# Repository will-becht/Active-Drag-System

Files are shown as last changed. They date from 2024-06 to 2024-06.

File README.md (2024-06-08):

# Active Drag System

## Table of Contents
- [Introduction](#introduction)
- [Flight Software](#flight-software)
- [PCB Design](#pcb-design)
- [OpenRocket](#openrocket)
- [CAD](#cad)
- [Installation](#installation)

## Introduction
This project is focused on the development of an active drag system, or air brake, for a model rocket competing in the NASA Student Launch competition (https://www.nasa.gov/learning-resources/nasa-student-launch/). This work was done on a non-competition vehicle as its advancements are intended to be used in future years' competitions.
This project demonstrates the designs of the various components, including the flight software, printed circuit board (PCB), OpenRocket analysis for the vehicle, and CAD drawings for the system. 
Due to time constraints and a focus on the main competition vehicle, the non-competition vehicle was never flown with an active drag system installed.

## Flight Software
### Overview
The `Arduino Codes` directory contains the code necessary for controlling the vehicle's Active Drag System. This system adjusts the vehicle's drag tabs based on readings from an altimeter and accelerometer to control the vehicle's apogee. The system is controlled before launch using a Bluetooth module that can connect to a user's phone, allowing for the constant monitoring of flight readiness once the system is installed in the vehicle. Data is redundantly saved to an onboard flash memory chip and SD for storage and post-flight analysis.

### Block Diagram
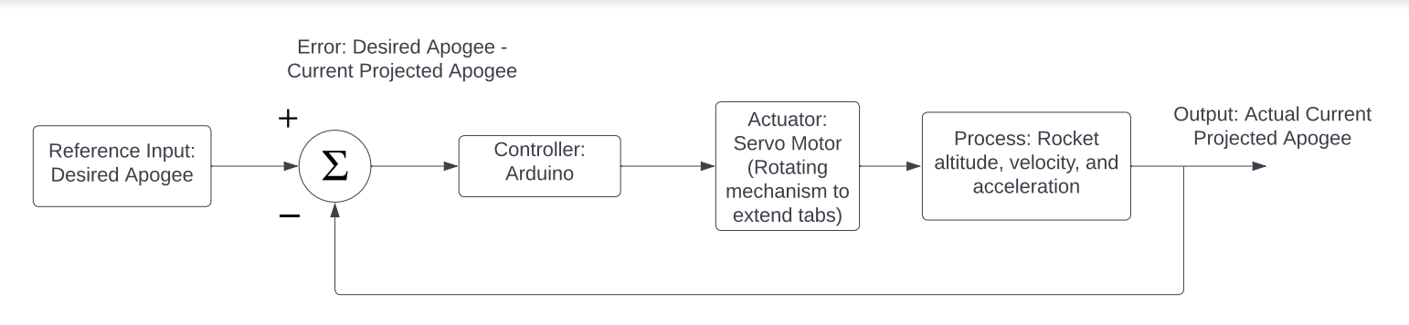
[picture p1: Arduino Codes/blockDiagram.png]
Flight Software


### Description
The flight software implements a state machine to manage the deployment of drag tabs in the Active Drag System. This system actively modulates the drag during flight to achieve a desired apogee by processing real-time data from the altimeter and accelerometer. The state machine ensures that the drag tabs are deployed or retracted based on the vehicle's altitude and acceleration, thus controlling the peak altitude accurately.

## PCB Design
### Overview
The `PCB Design` directory contains all the files related to the design and manufacturing of the vehicle's printed circuit boards (PCBs). These PCBs are used to integrate the electronic components necessary for the vehicle's operation.

### Images
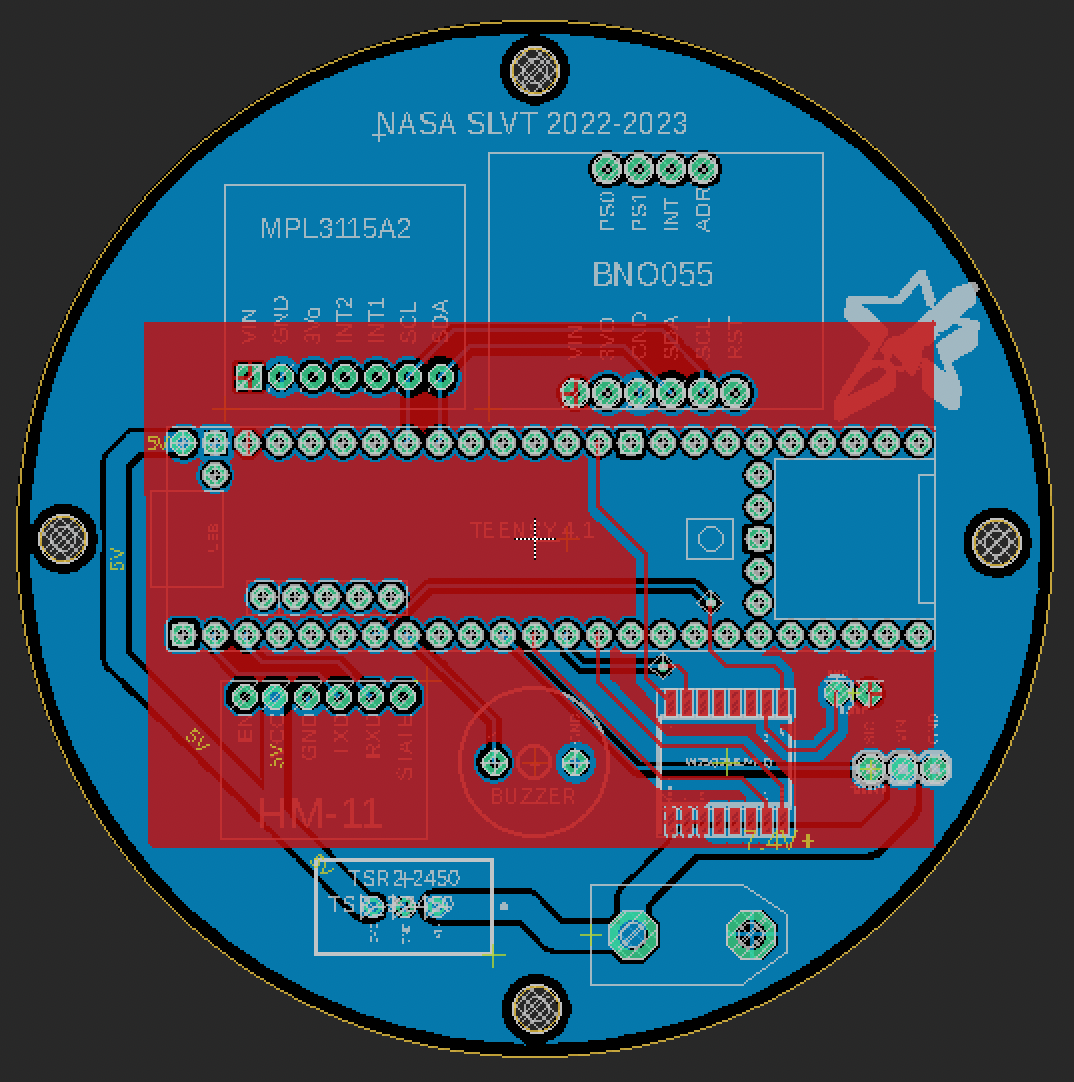
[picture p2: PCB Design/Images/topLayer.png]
Top Layer

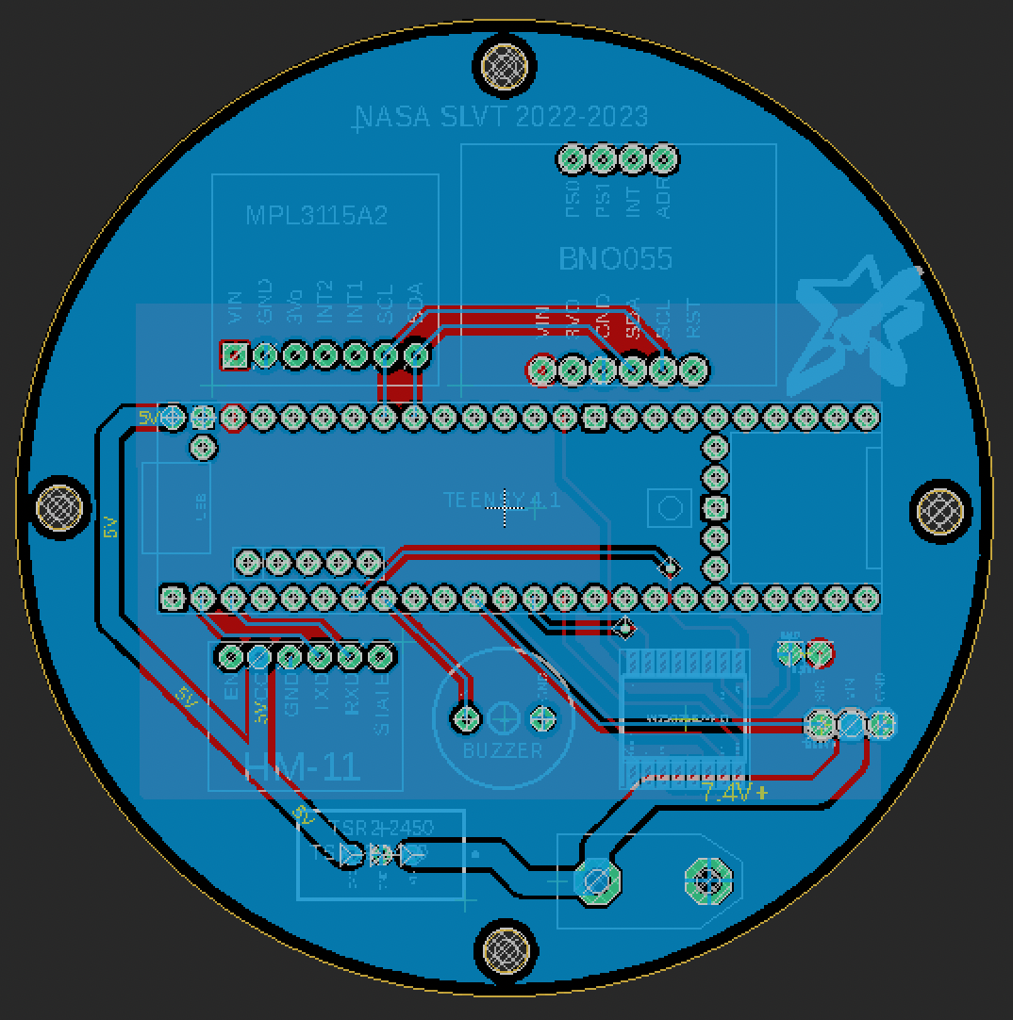
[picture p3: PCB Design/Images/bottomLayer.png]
Bottom Layer

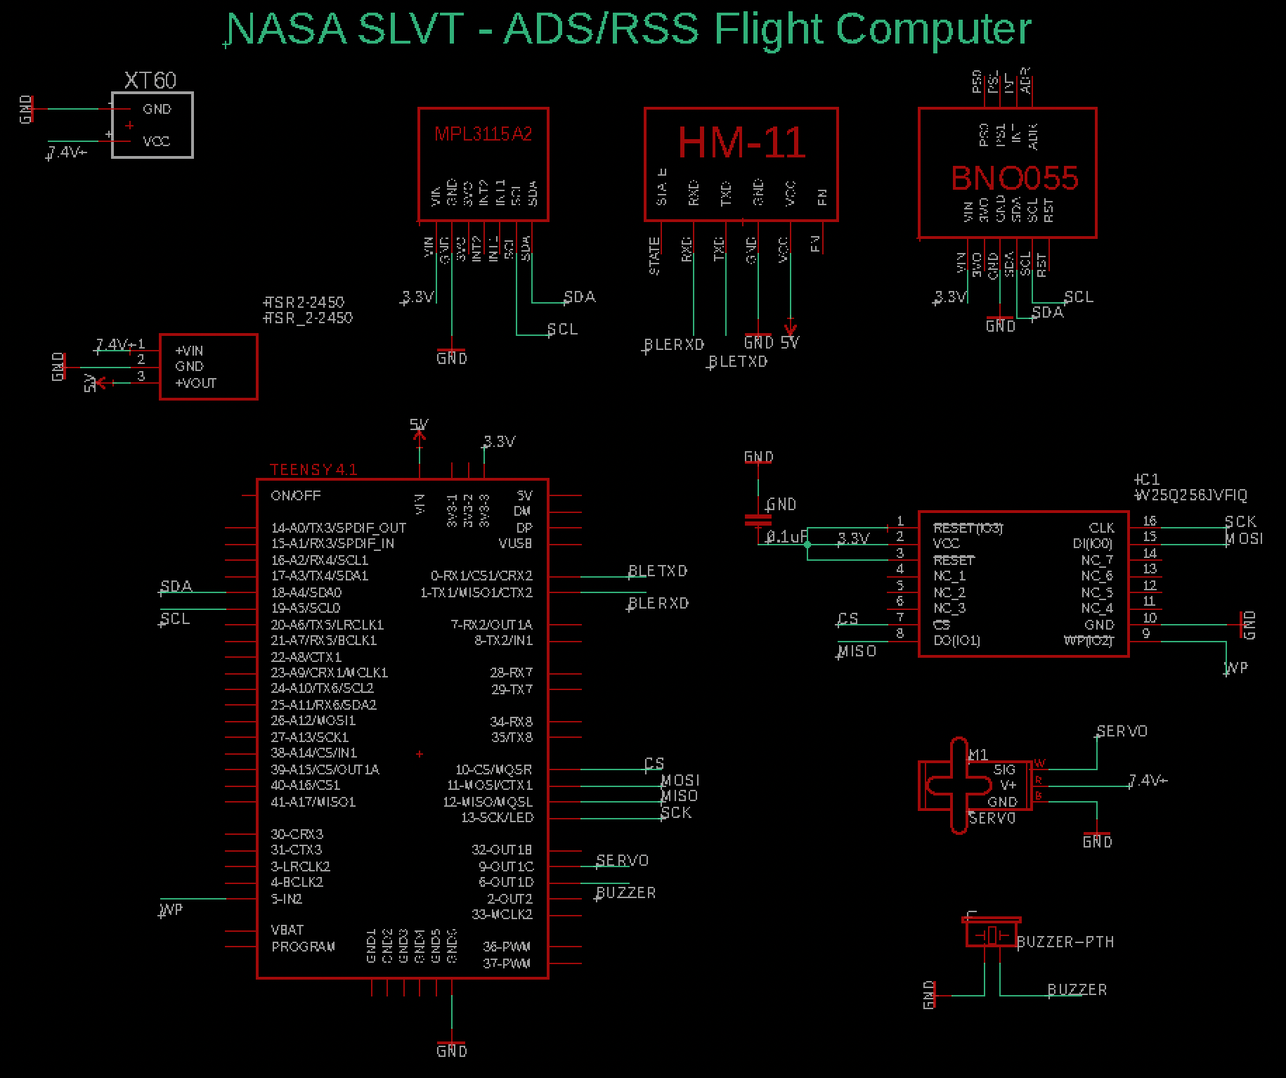
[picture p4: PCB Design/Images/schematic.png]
Schematic


### Description
PCB design is crucial for ensuring that the electronic components are connected properly. The files in this directory include design files, Gerber files for manufacturing, libraries for making the schematics, and images showing different layers and the schematic of the PCB. 

## OpenRocket
### Overview
The `OpenRocket` directory contains simulation files for the vehicle. These files can be used to simulate the vehicle's flight characteristics and performance.

### Images
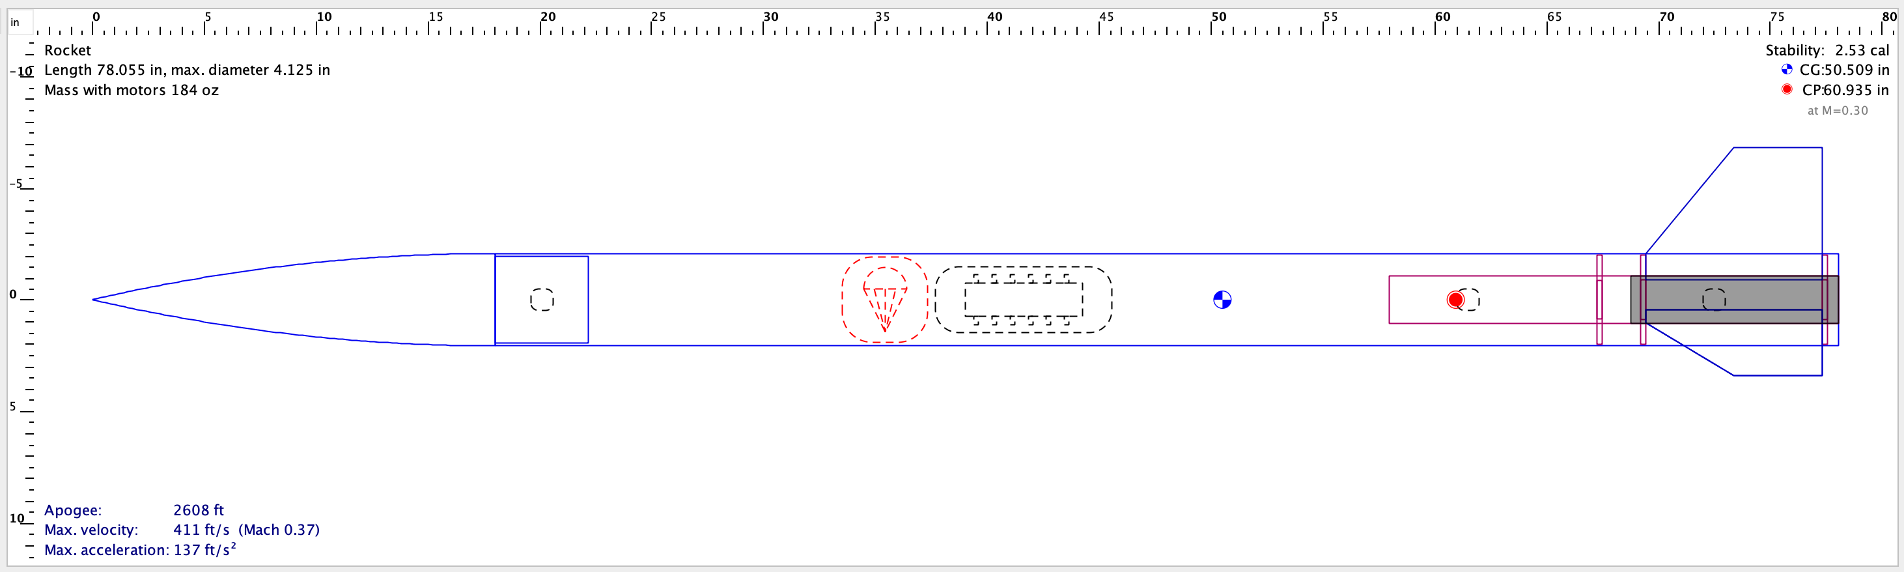
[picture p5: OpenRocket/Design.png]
Vehicle Design

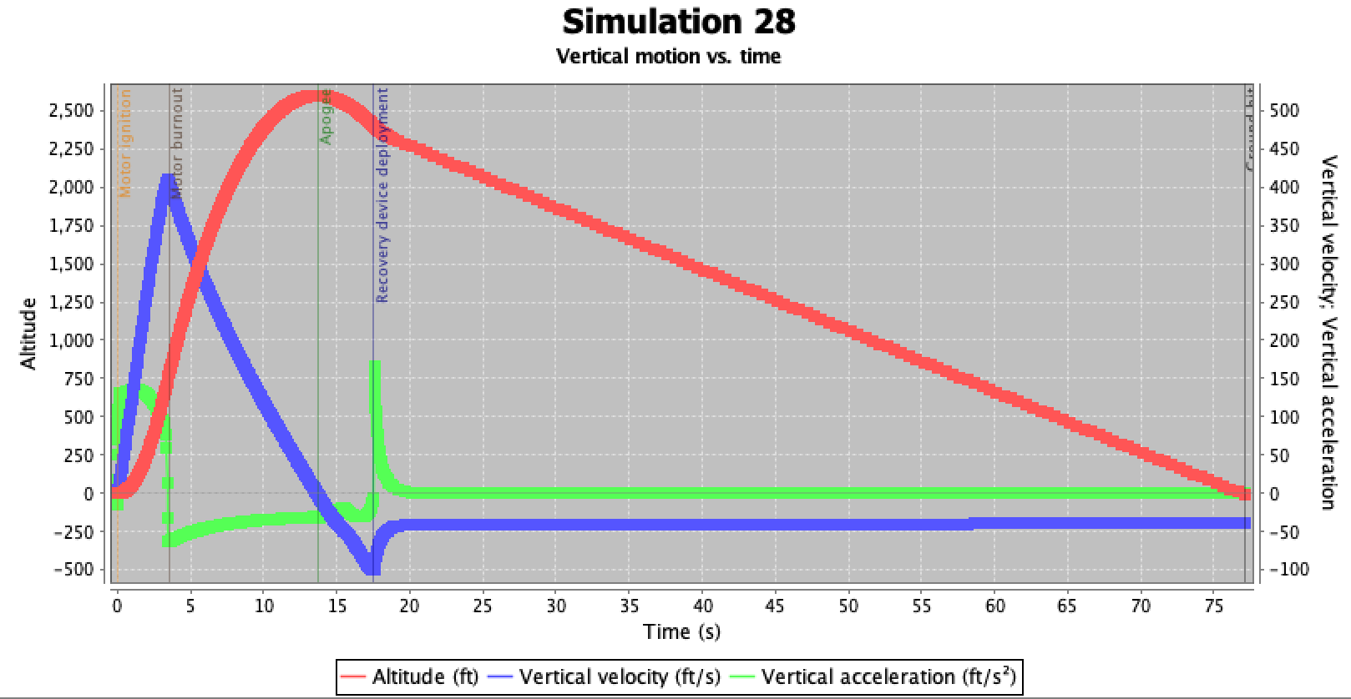
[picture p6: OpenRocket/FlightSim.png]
Flight Simulation


### Description
OpenRocket is a model rocket simulator that allows you to design and simulate the performance of rockets. The model in this directory represents the vehicle design as well as detailed simulations that help in predicting the flight path, stability, and performance of the vehicle.

## CAD
### Overview
The `CAD` directory contains the design files for the system's structural components. This model was created in SolidWorks, and the files can be used to fabricate the parts using 3D printing.

### Images
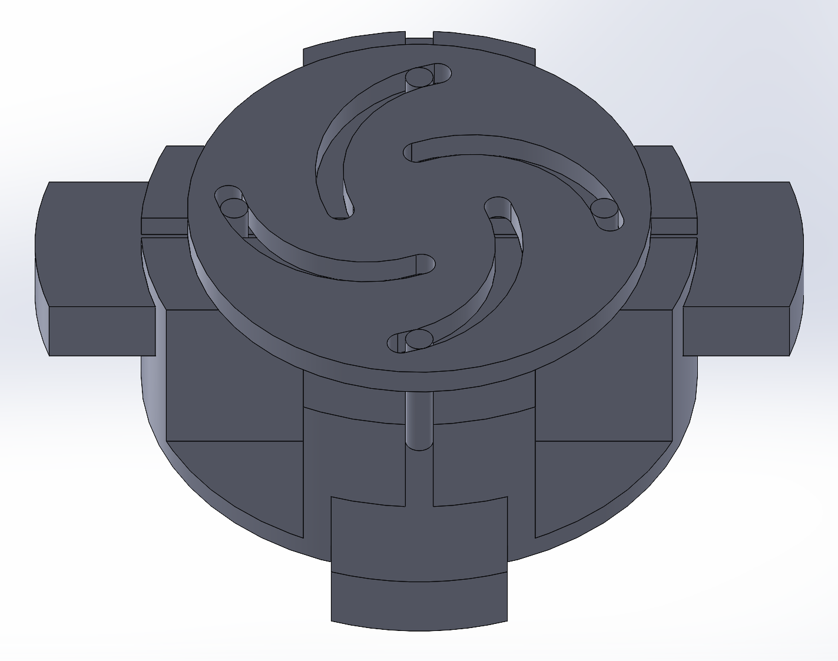
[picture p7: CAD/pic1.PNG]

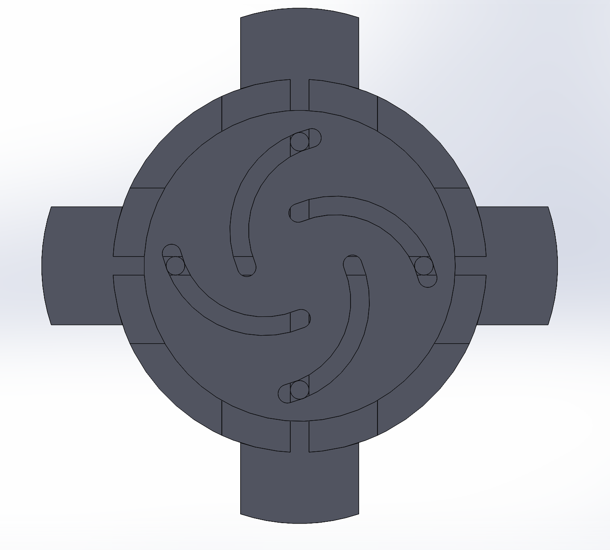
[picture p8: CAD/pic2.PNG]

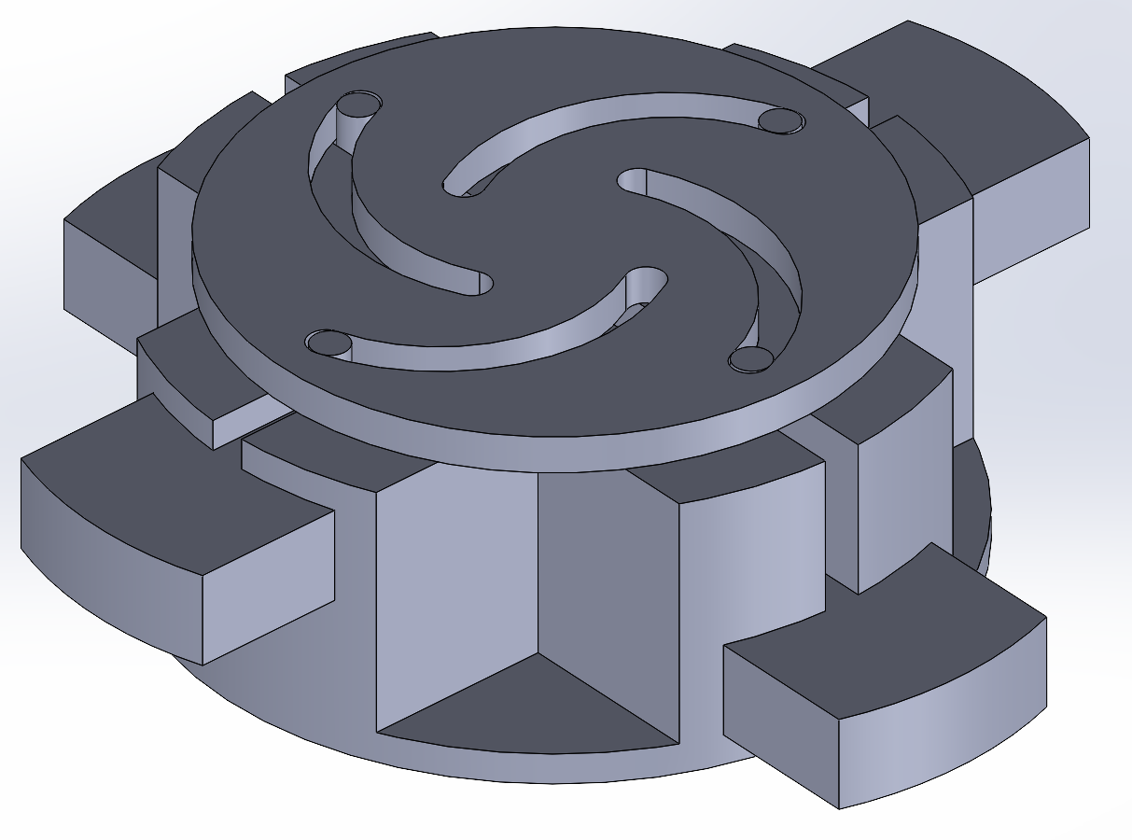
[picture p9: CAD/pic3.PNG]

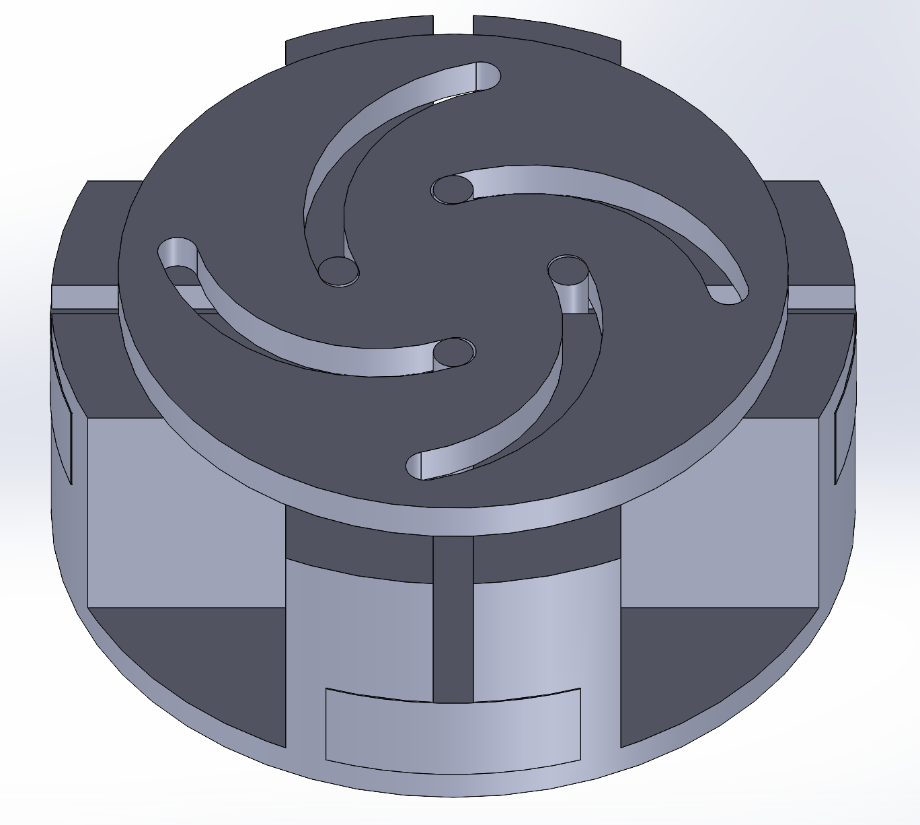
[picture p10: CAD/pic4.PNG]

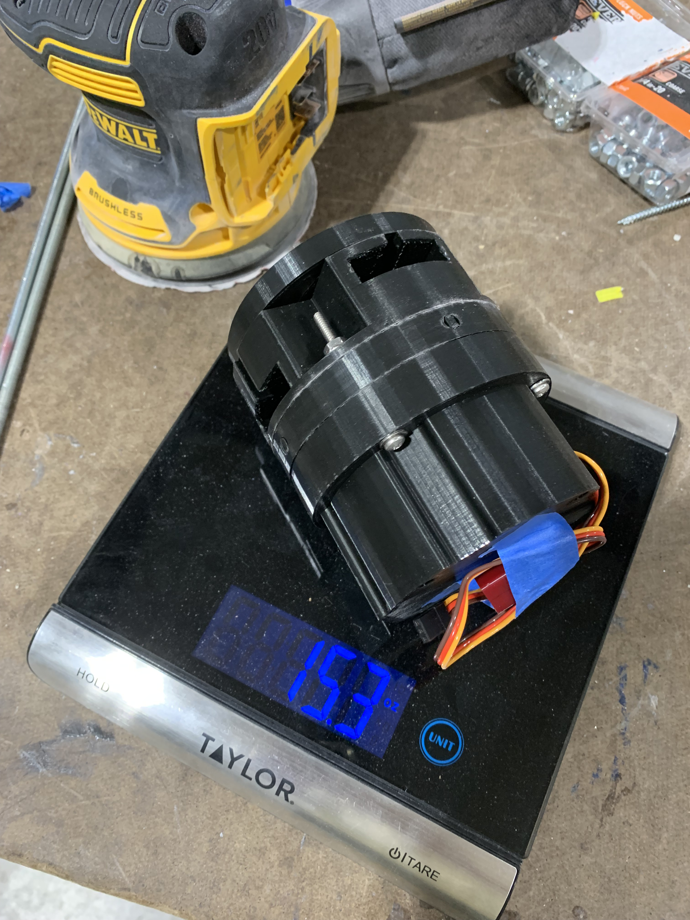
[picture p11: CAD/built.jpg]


### Description
FEA (finite element analysis) and CFD (computational fluid dynamics) were performed on the system to evaluate both its structural integrity and effectiveness as a braking system.

## Installation
To install the software and code for this project, follow these steps:

1. Clone the repository:
   ```bash
   git clone https://github.com/will-becht/Active-Drag-System

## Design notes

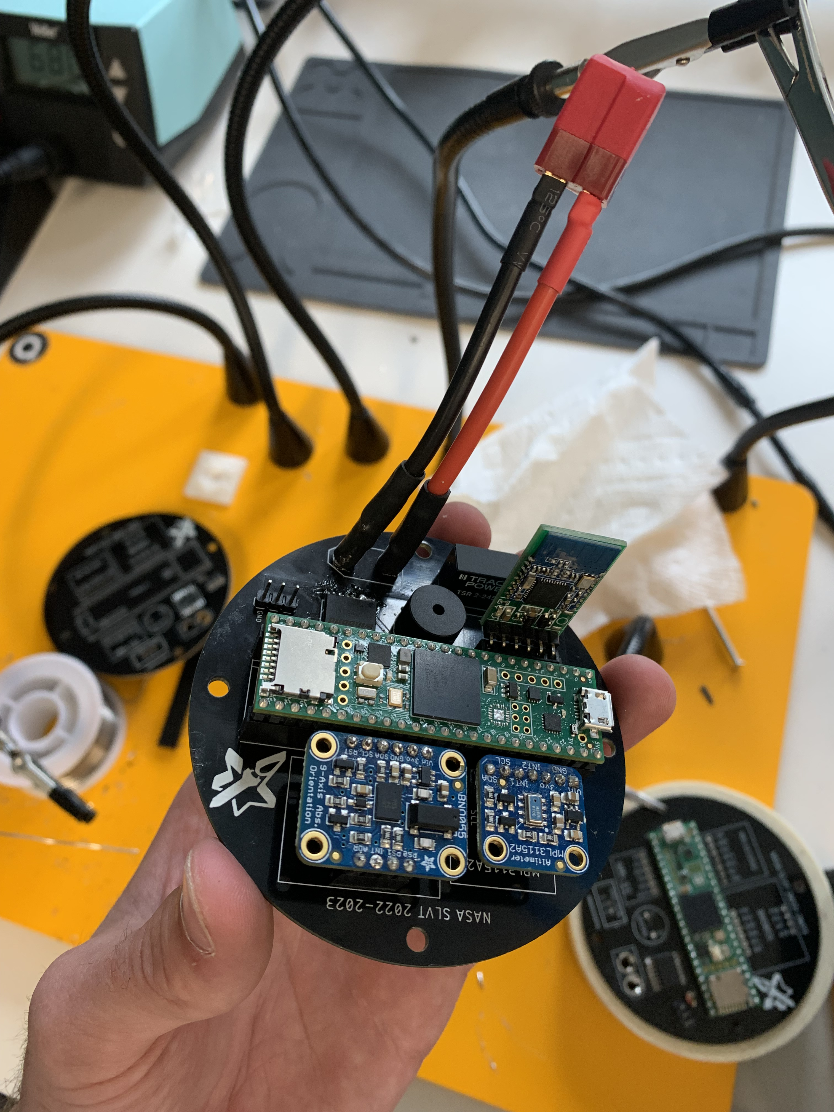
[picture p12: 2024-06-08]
PCB Design/Images/built.jpg

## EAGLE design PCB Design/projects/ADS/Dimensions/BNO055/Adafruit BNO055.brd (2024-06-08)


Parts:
C1, C2: 22pF; 0805-NO
C3: 0.1uF; 0805-NO
C4: 0.1uF; 0805_10MGAP
C5: 10uF; 0805-NO
C6: 10uF; 0805_10MGAP
D1: 1n4148; SOD-323
FID1, FID2: FIDUCIAL""; FIDUCIAL_1MM
JP1: HEADER-1X676MIL; 1X06_ROUND_76
JP2: HEADER-1X476MIL; 1X04_ROUND_76
Q1, Q2: BSS138; SOT23-WIDE
R3, R4, R5, R6, R7, R10: 10K; 0805-NO
R8, R9: 10K; _0805MP
U1: MIC5225-3.3; SOT23-5
U$2: BNO055
U$29, U$30, U$31, U$32: MOUNTINGHOLE2.5_THICK; MOUNTINGHOLE_2.5_PLATED_THICK
Y1: 32.768kHz; CRYSTAL_8X3.8

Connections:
3.3V: C4.2, C6.1, JP1.2, Q1.1 (G), Q2.1 (G), R6.2, R7.2, R10.2, U1.5 (OUT), U$2.3 (VDD), U$2.4 (NBOOT_LOAD_PIN), U$2.28 (VDDIO)
5.0V: C5.1, JP1.1, R8.2, R9.2, U1.1 (IN), U1.3 (EN)
GND: C1.1, C2.1, C3.1, C4.1, C5.2, C6.2, JP1.3, R3.2, R4.2, R5.2, U1.2 (GND), U$2.2 (GND), U$2.10 (PIN10(GND)), U$2.15 (PIN15(GND)), U$2.16 (PIN16(GND)), U$2.18 (COM2(GND)), U$2.25 (GND)
I2CADDR_3V: JP2.4, R5.1, U$2.17 (COM3/I2C_ADDR)
INT_3V: JP2.3, U$2.14 (INT)
unnamed: C1.2, U$2.27 (XIN32), Y1.P$4 (2)
unnamed: C2.2, U$2.26 (XOUT32), Y1.P$1 (1)
unnamed: C3.2, U$2.9 (CAP)
NRESET_3V: D1.A, R10.1, U$2.11 (NRESET)
PS0_3V: JP2.1, R3.1, U$2.6 (PS0)
PS1_3V: JP2.2, R4.1, U$2.5 (PS1)
RST_5V: D1.C, JP1.6
SCL_3V: Q2.2 (S), R7.1, U$2.19 (COM1/SCL/RX)
SCL_5V: JP1.5, Q2.3 (D), R9.1
SDA_3V: Q1.2 (S), R6.1, U$2.20 (COM0/SDA/TX)
SDA_5V: JP1.4, Q1.3 (D), R8.1



Board: 2 copper layers, 26.7 x 20.3 mm, 31 parts (2 on the bottom side), 16 nets.

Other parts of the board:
U$3: PCBFEAT-REV-040
U$28: ADAFRUIT_TEXT_20MM
U$33: ADAFRUIT_2.5MM

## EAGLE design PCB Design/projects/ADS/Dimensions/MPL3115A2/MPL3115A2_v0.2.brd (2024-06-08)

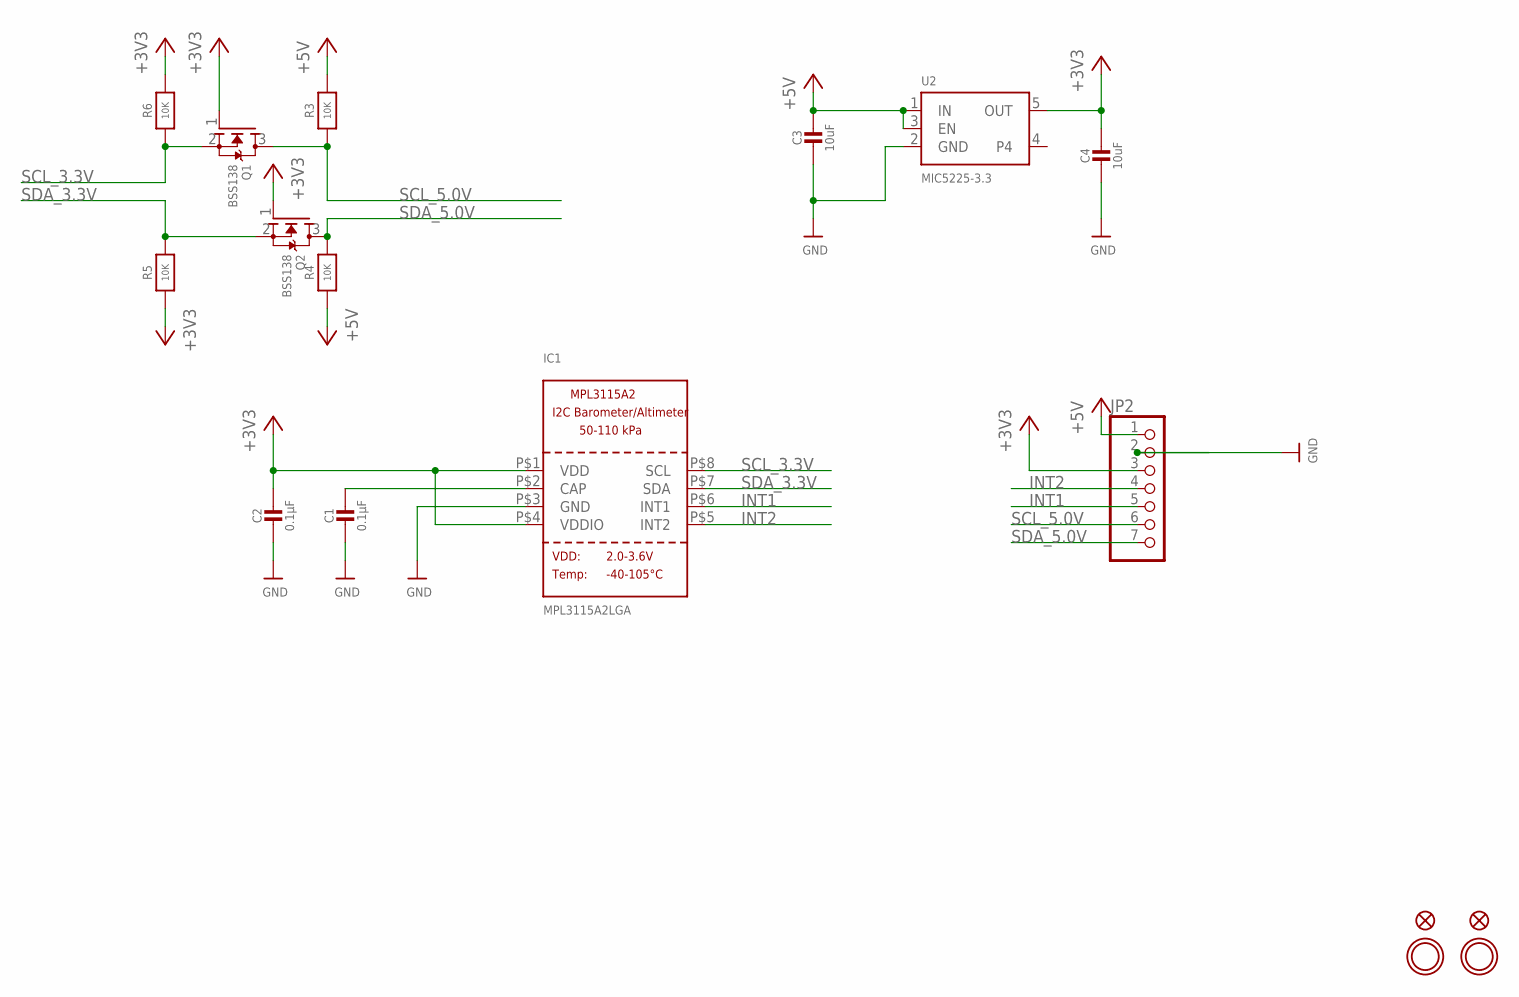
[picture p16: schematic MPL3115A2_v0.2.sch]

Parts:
C1, C2: 0.1µF; 0805-NO
C3, C4: 10uF; 0805-NO
FID1, FID2: FIDUCIAL""; FIDUCIAL_1MM
IC1: MPL3115A2LGA; LGA8
JP2: HEADER-1X770MIL; 1X07_ROUND_70
Q1, Q2: BSS138; SOT23-WIDE
R3, R4, R5, R6: 10K; 0805-NO
U2: MIC5225-3.3; SOT23-5
U$8, U$9: MOUNTINGHOLE2.5; MOUNTINGHOLE_2.5_PLATED

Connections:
+3V3: C2.1, C4.1, IC1.P$1 (VDD), IC1.P$4 (VDDIO), JP2.3, Q1.1 (G), Q2.1 (G), R5.1, R6.2, U2.5 (OUT)
+5V: C3.1, JP2.1, R3.2, R4.1, U2.1 (IN), U2.3 (EN)
CAP: C1.1, IC1.P$2 (CAP)
GND: C1.2, C2.2, C3.2, C4.2, IC1.P$3 (GND), JP2.2, U2.2 (GND)
INT1: IC1.P$6 (INT1), JP2.5
INT2: IC1.P$5 (INT2), JP2.4
SCL_3.3V: IC1.P$8 (SCL), Q1.2 (S), R6.1
SCL_5.0V: JP2.6, Q1.3 (D), R3.1
SDA_3.3V: IC1.P$7 (SDA), Q2.2 (S), R5.2
SDA_5.0V: JP2.7, Q2.3 (D), R4.2

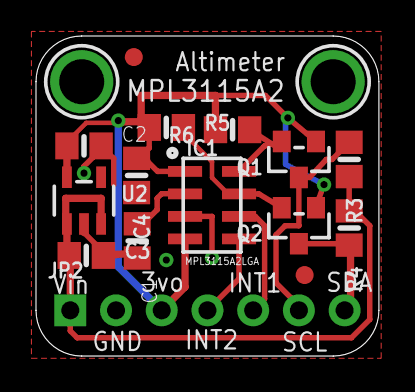
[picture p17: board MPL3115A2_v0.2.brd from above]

Board: 2 copper layers, 19.1 x 17.8 mm, 18 parts (1 on the bottom side), 10 nets.

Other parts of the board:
U$14: ADAFRUIT_3.5MM

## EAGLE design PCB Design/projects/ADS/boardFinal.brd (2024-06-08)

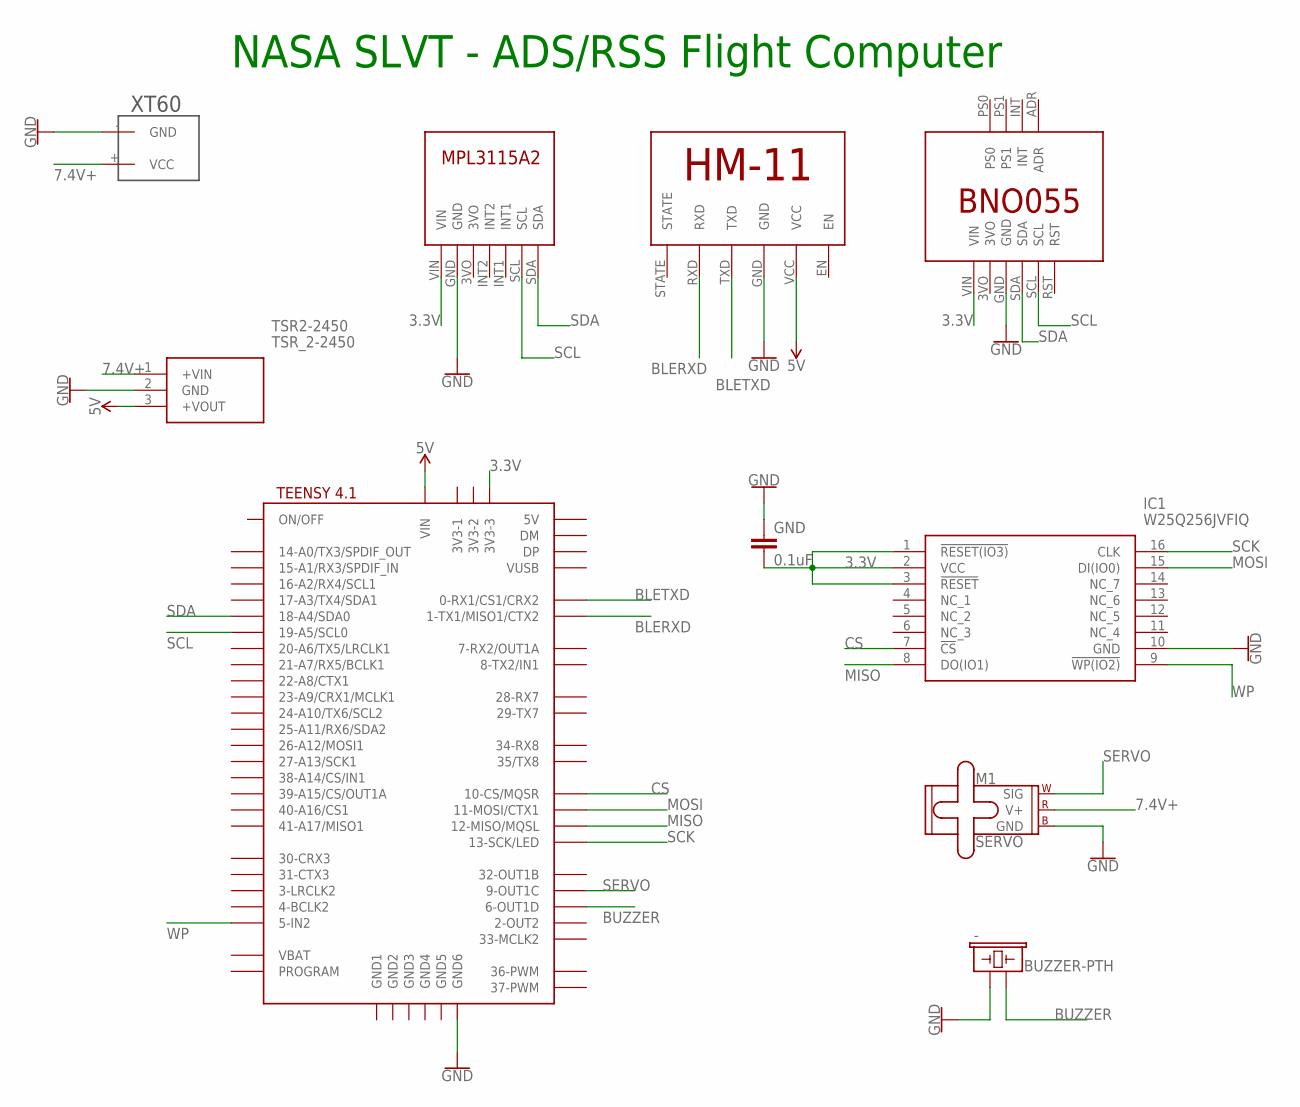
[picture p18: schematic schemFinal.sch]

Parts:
-: BUZZER-PTH; BUZZER-12MM
GND: 0.1uF; CAP-PTH-2.54
IC1: W25Q256JVFIQ; SOIC127P1032X264-16N
M1: SERVO; 1X03
TSR2-2450: TSR_2-2450; TSR-2
U$1: BNO055
U$2: MPL3115A2
U$3: TEENSY41-E; TENNSY41-E
U$4: HM-11
U$5: XT60

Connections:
3.3V: GND.2, IC1.1 (!RESET(IO3)), IC1.2 (VCC), IC1.3 (!RESET), U$1.VIN, U$2.VIN, U$3.3V3-3
5V: TSR2-2450.3 (+VOUT), U$3.VIN, U$4.VCC
7.4V+: M1.2 (V+), TSR2-2450.1 (+VIN), U$5.+ (VCC)
BLERXD: U$3.1-TX1/MISO1/CTX2, U$4.RXD
BLETXD: U$3.0-RX1/CS1/CRX2, U$4.TXD
BUZZER: -.- (2), U$3.6-OUT1D
CS: IC1.7 (!CS), U$3.10-CS\MQSR (10-CS/MQSR)
GND: -.+ (1), GND.1, IC1.10 (GND), M1.3 (GND), TSR2-2450.2 (GND), U$1.GND, U$2.GND, U$3.GND6, U$4.GND, U$5.- (GND)
MISO: IC1.8 (DO(IO1)), U$3.12-MISO/MQSL
MOSI: IC1.15 (DI(IO0)), U$3.11-MOSI/CTX1
SCK: IC1.16 (CLK), U$3.13-SCK/LED
SCL: U$1.SCL, U$2.SCL, U$3.19-A5/SCL0
SDA: U$1.SDA, U$2.SDA, U$3.18-A4/SDA0
SERVO: M1.1 (SIG), U$3.9-OUT1C
WP: IC1.9 (!WP(IO2)), U$3.5-IN2

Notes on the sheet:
NASA SLVT - ADS/RSS Flight Computer

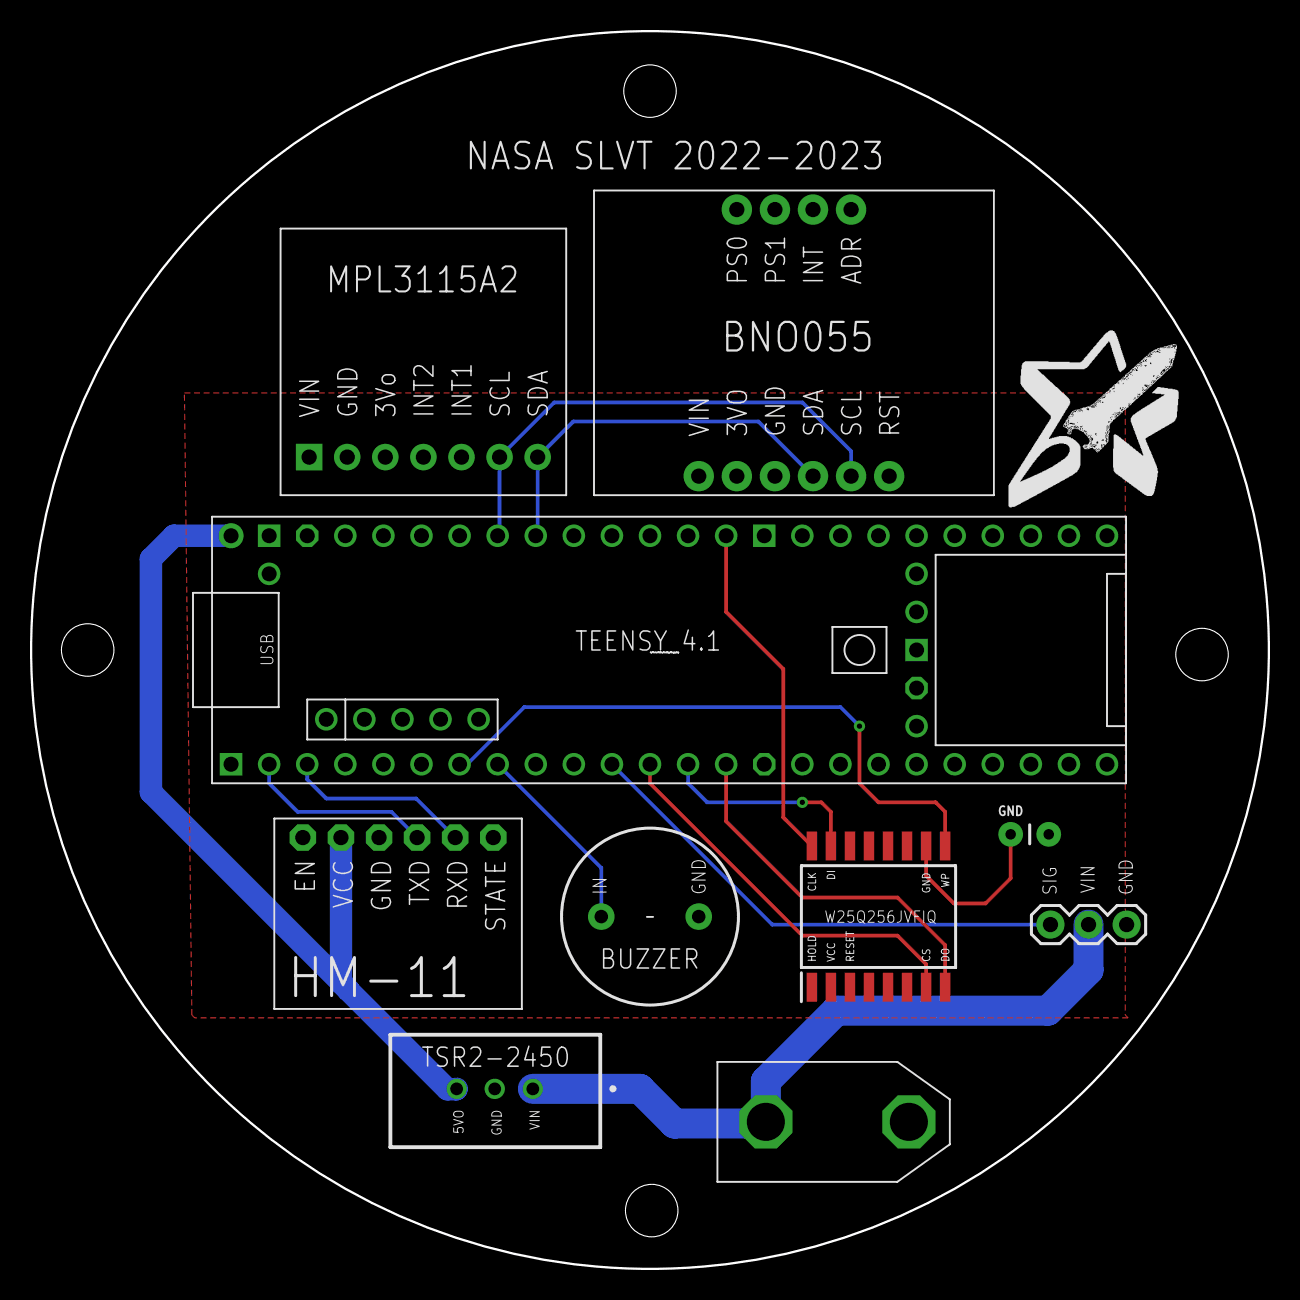
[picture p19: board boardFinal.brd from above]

Board: 2 copper layers, 82.5 x 82.5 mm, 10 parts (0 on the bottom side), 15 nets.

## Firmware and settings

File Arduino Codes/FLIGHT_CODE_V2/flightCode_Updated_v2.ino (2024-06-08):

// ***** LIBRARIES ***** //
#include <Adafruit_BNO055.h>
#include <Adafruit_MPL3115A2.h>
#include <Adafruit_Sensor.h>
#include <LittleFS.h>
#include <Servo.h>
#include <SoftwareSerial.h>
#include <utility/imumaths.h>
#include <Wire.h>
#include <SD.h>
#include <SPI.h>
// ********** //


// ***** INITIALIZING VARIABLES ***** //
// Delays for sample rates
#define BNO055_SAMPLERATE_DELAY_MS (100)
#define MPL3115A2_SAMPLERATE_DELAY_MS (250)

// IMU
Adafruit_BNO055 myIMU = Adafruit_BNO055();
uint8_t systemCal, gyroCal, accCal, magCal = 0;
imu::Vector<3> acc, gyro, mag, euler, linearAccel, gravity;
imu::Quaternion quat;
int8_t imuTemp;

// ALTIMETER
Adafruit_MPL3115A2 baro;
float pressure;
float altitude;
float temperature;
float sensorSampleDelay;

// Flash Chip
LittleFS_SPIFlash myfs;
const int chipSelect = 10;
File dataFile;
char dataFn[16];
char SDdataFn[16];
bool writing = false;
bool writeHeader = true;

// SD CARD
const int chipSelectSD = BUILTIN_SDCARD;

// Servo
Servo myServo;
int maxServoMicro = 1200;
int minServoMicro = 1000;

// State changing conditions
const float g = 9.8;
const float liftOffGThreshold = -3;
const float liftOffHThreshold = 10;
const float burnOutThreshold = 0;
const float burnOutTime = 5000; // in milli seconds
const float apogeeTime = 15000; // in milli seconds
const float apogeeTolerance = 5; // in meters
int missionPhase = 1; // STANDBY, PAD, BOOST, COAST, APOGEE, DONE
float startTime = 0;
float burnTime = 0;
float coastTime = 0;
float apogeeAlti = 0;
float onPadAlti = 1000000;

// Bluetooth
SoftwareSerial mySerial(0, 1);

// Buzzer
int buzzer = 6;

// Testing
bool testMode = true; 
// ********** //


// ***** CONNECTING SERIAL PORTS AND INITIALIZING SENSORS ***** //
void setup() {
  pinMode(buzzer, OUTPUT);
  myServo.attach(9);
  mySerial.begin(9600);
  while (!mySerial) {
    ; // wait for serial port to connect.
  }

  if (!myfs.begin(chipSelect)) {
    while (1) {
      // Error, so don't do anything more - stay stuck here
    }
  }
  //dataFn = String(random(100000000),DEC) + ".txt";
  int num = random(10000000);
  itoa(num, dataFn, 10);
  dataFile = myfs.open(dataFn, FILE_WRITE);
  

  if (!baro.begin()) {
    while (1);
  }
  //baro.setSeaPressure(1013.26);
  baro.setSeaPressure(1030);

  if (!myIMU.begin()) {
    while (1);
  }
  myIMU.setExtCrystalUse(true);

  playBuzzer(1500);
}

void loop() {     
  // READ IN DATA FROM IMU
  myIMU.getCalibration(&systemCal, &gyroCal, &accCal, &magCal);
  acc = myIMU.getVector(Adafruit_BNO055::VECTOR_ACCELEROMETER);
  gyro = myIMU.getVector(Adafruit_BNO055::VECTOR_GYROSCOPE);
  mag = myIMU.getVector(Adafruit_BNO055::VECTOR_MAGNETOMETER);
  euler = myIMU.getVector(Adafruit_BNO055::VECTOR_EULER);
  linearAccel = myIMU.getVector(Adafruit_BNO055::VECTOR_LINEARACCEL);
  gravity = myIMU.getVector(Adafruit_BNO055::VECTOR_GRAVITY);
  quat = myIMU.getQuat();
  imuTemp = myIMU.getTemp();

  // READ IN DATA FROM BARO
  pressure = baro.getPressure();
  altitude = baro.getAltitude() - onPadAlti;
  temperature = baro.getTemperature();
  sensorSampleDelay = millis();

  // SAVE DATA TO FLASH CHIP
  if (writing) {
    if (dataFile) {
      saveData();
    } else {
      mySerial.print("Error Saving Data");
    }
  }

  int i;
  if (mySerial.available()) {
    i = mySerial.read();
    bluetoothCommand(i);
  }
  
  // ACT ACCORDING TO MISSION PHASE
  switch (missionPhase) {
                                                        // *** PHASE 1: STANDBY *** // (NO DATA SAVED)
    case 1:
      if (writing) {
        writing = false;
        mySerial.write("Stopped Logging Data");
      }
      break;

                                                        // *** PHASE 2: ON PAD *** // (RECORDING DATA, WILL SHIFT PHASES DEPENDING ON ALT AND ACC)
    case 2:
      if (!writing) {
        writing = true;
        mySerial.write("Started Logging Data");
      }
      if (acc[2] <= g*liftOffGThreshold && altitude >= liftOffHThreshold) {
        missionPhase = 3;
        burnTime = millis();
      }
      // test mode
      if (testMode && millis() - startTime >= 10*1000) {
        missionPhase = 3;
        burnTime = millis();
      }
      break;

                                                        // *** PHASE 3: MOTOR BURN *** // (RECORDING DATA, WILL SHIFT PHASES DEPENDING ON ACC AND burnOutTime)
    case 3:
      if (acc[2] >= g*burnOutThreshold || millis() - burnTime >= burnOutTime) {
        missionPhase = 4;
        coastTime = millis();
      }
      break;

                                                        // *** PHASE 4: COAST *** // (DEPLOYING AIRBRAKES, WILL SHIFT PHASES DEPENDING ON ALT and apogeeTime)
    case 4:
      if (altitude > apogeeAlti) {
          apogeeAlti = altitude;
      }
      if (apogeeAlti - altitude >= apogeeTolerance || millis() - coastTime >= apogeeTime) {
          missionPhase = 5;
      }
      // deploy airbrakes until apogee
      myServo.writeMicroseconds(maxServoMicro);
      break;

                                                        // *** PHASE 5: APOGEE *** // (RETRACT TABS)
    case 5:
      myServo.writeMicroseconds(minServoMicro);
      break;
    
                                                        // *** PHASE 6: DONE *** // (LAUNCH VEHICLE ON GROUND)
    case 6:
      if (writing) {
        mySerial.write("Stopped Logging Data");
        writing = false;
      }
      break;
    default:
      break;
  }

  // Delaying based on sensor sample rate
  if (sensorSampleDelay > millis()) {
    delay(sensorSampleDelay - millis());
  }
}

// BLUETOOTH COMMANDS
void bluetoothCommand(int i) {
  switch (i) {
    case '1':
      sendCal();
      break;
    case '2':
      sendBaro();
      sendAcc();
      break;
    case '3':
      mySerial.write("Beginning Servo Test");
      myServo.writeMicroseconds(minServoMicro);
      delay(2000);
      myServo.writeMicroseconds(maxServoMicro);
      break;
    case '4':
      missionPhase = 1;
      mySerial.write("STANDBY Phase Initiated");
      break;
    case '5':
      missionPhase = 2;
      startTime = millis();
      mySerial.write("PAD Phase Initiated, Ready for Launch");
      break;
    case '6':
      mySerial.write("Current Mission Phase: ");
      mySerial.print(missionPhase);
      break;
    case '7':
      mySerial.write("Initalizing altimeter\n");
      onPadAlti = initializeAltitude();
      mySerial.write("Ground Altitude: ");
      mySerial.print(onPadAlti);
      break;
    case '8':
      mySerial.write("Menu:\n");
      mySerial.write("1. Calibration, 2. Altimeter, IMU, 3. Servo Test, 4. Phase 1, 5. Phase 2, 6. Current Phase, 7. Set Altimeter, 8. Menu");
      break;
    default:
      break;
  }
}

// SETTING GROUND ALTITUDE
float initializeAltitude() {
  int t = millis();
  int count = 0; 
  float sum = 0;
  while (millis() - t < 20.0*1000.0) {
    sum = sum+baro.getAltitude();
    count ++;
  }
  return sum/count;
}

// SAVING DATA 
void saveData() {
  if (writeHeader) {
    dataFile.println("time,accCal,gyroCal,magCal,systemCal,accX,accY,accZ,gyroX,gyroY,gyroZ,magX,magY,magZ,eulerX,eulerY,eulerZ,linearAccelX,linearAccelY,linearAccelZ,gravityX,gravityY,gravityZ,quatW,quatX,quatY,quatZ,imuTemp,baroTemp,pressure,altitude,missionPhase,onPadAlti");
    writeHeader = false;
  }

  // TIMESTAMP
  dataFile.print(millis());
  dataFile.write(",");
  
  // IMU CALIBRATION
  dataFile.print(accCal);
  dataFile.write(",");
  dataFile.print(gyroCal);
  dataFile.write(",");
  dataFile.print(magCal);
  dataFile.write(",");
  dataFile.print(systemCal);
  dataFile.write(",");

  // ACCELEROMETER DATA(m/s^2)
  dataFile.print(acc.x());
  dataFile.write(",");
  dataFile.print(acc.y());
  dataFile.write(",");
  dataFile.print(acc.z());
  dataFile.write(",");

  // GYROSCOPE DATA(rps)
  dataFile.print(gyro.x());
  dataFile.write(",");
  dataFile.print(gyro.y());
  dataFile.write(",");
  dataFile.print(gyro.z());
  dataFile.write(",");

  // MAGNETOMETER DATA(uT)
  dataFile.print(mag.x());
  dataFile.write(",");
  dataFile.print(mag.y());
  dataFile.write(",");
  dataFile.print(mag.z());
  dataFile.write(",");

  // EULER DATA
  dataFile.print(euler.x());
  dataFile.write(",");
  dataFile.print(euler.y());
  dataFile.write(",");
  dataFile.print(euler.z());
  dataFile.write(",");

  // LINEAR ACCELERATION DATA(m/s^2)
  dataFile.print(linearAccel.x());
  dataFile.write(",");
  dataFile.print(linearAccel.y());
  dataFile.write(",");
  dataFile.print(linearAccel.z());
  dataFile.write(",");

  // GRAVITY DATA(m/s^2)
  dataFile.print(gravity.x());
  dataFile.write(",");
  dataFile.print(gravity.y());
  dataFile.write(",");
  dataFile.print(gravity.z());
  dataFile.write(",");

  // QUATERNION DATA
  dataFile.print(quat.w(), 4);
  dataFile.write(",");
  dataFile.print(quat.x(), 4);
  dataFile.write(",");
  dataFile.print(quat.y(), 4);
  dataFile.write(",");
  dataFile.print(quat.z(), 4);
  dataFile.write(",");

  // TEMPERATURE DATA (degC)
  dataFile.print(imuTemp);
  dataFile.write(",");
  dataFile.print(temperature);
  dataFile.write(",");

  // ALTITUDE DATA
  dataFile.print(pressure); 
  dataFile.write(",");
  dataFile.print(altitude); 

  // MISSION PHASE
  dataFile.write(",");
  dataFile.print(missionPhase);

  // ON PAD ALTITUDE
  dataFile.write(",");
  dataFile.println(onPadAlti);
}

// Sending Calibration Data to Phone
void sendCal() {
  mySerial.write("A: ");
  mySerial.print(accCal);
  mySerial.write(", G: ");
  mySerial.print(gyroCal);
  mySerial.write(", M: ");
  mySerial.print(magCal);
  mySerial.write(", S: ");
  mySerial.print(systemCal);
}

// Sending Altimeter Data to Phone
void sendBaro() {
  mySerial.write("P: ");
  mySerial.print(pressure); // hPa
  mySerial.write(", A: ");
  mySerial.print(altitude); // m
  mySerial.write(", T: ");
  mySerial.print(temperature); // deg C
}

// Sending Accelerometer Data to Phone
void sendAcc() {
  mySerial.write("X: ");
  mySerial.print(acc.x());
  mySerial.write(", Y: ");
  mySerial.print(acc.y());
  mySerial.write(", Z: ");
  mySerial.print(acc.z());
}

void playBuzzer(int t) {
  tone(buzzer, 1000); 
  delay(t);
  noTone(buzzer);
}

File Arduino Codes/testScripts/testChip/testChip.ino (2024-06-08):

/*
  |~~~~~~~~~~~~~~~~~~~~~~~~~~~~~~~~~~~~~~~~~~~~~~~~~~~~~~~~~~~~~~~~~~~~~~~~~~~~~~~~~~~~~~~~~~~~~~~~~~~~~~~~~~~~~~~~~~~~~~~~~~~~~~~~~~~~~~~~~~~~~~~|
  |                                                               Struct_writer.ino                                                               |
  |                                                               SPIMemory library                                                                |
  |                                                                   v 3.1.0                                                                     |
  |~~~~~~~~~~~~~~~~~~~~~~~~~~~~~~~~~~~~~~~~~~~~~~~~~~~~~~~~~~~~~~~~~~~~~~~~~~~~~~~~~~~~~~~~~~~~~~~~~~~~~~~~~~~~~~~~~~~~~~~~~~~~~~~~~~~~~~~~~~~~~~~|
  |                                                                    Marzogh                                                                    |
  |                                                                  03.03.2018                                                                   |
  |~~~~~~~~~~~~~~~~~~~~~~~~~~~~~~~~~~~~~~~~~~~~~~~~~~~~~~~~~~~~~~~~~~~~~~~~~~~~~~~~~~~~~~~~~~~~~~~~~~~~~~~~~~~~~~~~~~~~~~~~~~~~~~~~~~~~~~~~~~~~~~~|
  |                                                                                                                                               |
  |                        This program writes a struct to a random location on your flash memory chip and reads it back.                         |
  |                                                                                                                                               |
  |~~~~~~~~~~~~~~~~~~~~~~~~~~~~~~~~~~~~~~~~~~~~~~~~~~~~~~~~~~~~~~~~~~~~~~~~~~~~~~~~~~~~~~~~~~~~~~~~~~~~~~~~~~~~~~~~~~~~~~~~~~~~~~~~~~~~~~~~~~~~~~~|
*/

#include<SPIMemory.h>

#define NUMBEROFREPEATS 100
#define BAUD_RATE 9600
#define LDR A0
SPIFlash flash(10);

struct ConfigurationIn {
  float lux = 3.24;
  float vOut = 4.45;                    // Voltage ouput from potential divider to Analog input
  float RLDR = 1.234;                   // Resistance calculation of potential divider with LDR
  bool light = true;
  uint8_t adc = 45;
  uint8_t arr[8] = {0, 1, 2, 3, 4, 5, 6, 7};
  struct MISC {
    byte tempHigh = 30;
    byte tempLow = 20;
    bool parkingMode = false;
    bool allowDataToBeSent = false;
  } misc;
  struct NETWORK {
    char ssid[5] = "ssid";
    char pwd[4] = "pwd";
    char userid[7] = "userid";
  } network;
  struct CHARGING_INFO {
    byte interval = 5;
    byte highChargingDefault = 80;
  } charging;
};
ConfigurationIn configurationIn;

struct ConfigurationOut {
  float lux;
  float vOut;                   // Voltage ouput from potential divider to Analog input
  float RLDR;                   // Resistance calculation of potential divider with LDR
  bool light;
  uint8_t adc;
  uint8_t arr[8];
  struct MISC {
    byte tempHigh;
    byte tempLow;
    bool parkingMode;
    bool allowDataToBeSent;
  } misc;
  struct NETWORK {
    char ssid[5];
    char pwd[4];
    char userid[7];
  } network;
  struct CHARGING_INFO {
    byte interval;
    byte highChargingDefault;
  } charging;
};
ConfigurationOut configurationOut;
uint16_t eraseCount, writeCount, errorCount, readCount;

void setup() {
  Serial.begin(9600);
  eraseCount = 0;
  writeCount = 0;
  errorCount = NUMBEROFREPEATS;
  readCount = 0;
  randomSeed(analogRead(LDR));
  Serial.print(F("Initialising Flash memory"));
  for (int i = 0; i < 10; ++i)
  {
    Serial.print(F("."));
  }
  Serial.println();
  flash.begin();
  Serial.println();
#ifdef PRINTINDIVIDUALRUNS
  printLine();
  Serial.println();
  Serial.print("\tStruct number\t\t\tSection Erase\t\t\tStruct Write\t\t\tErrorCheck\t\t\tStruct Read\t\t\t");
  Serial.println();
  printLine();
  Serial.println();
#endif

  for (uint16_t x = 1; x <= NUMBEROFREPEATS; x++) {
    Serial.println(x);
    //uint32_t _addr = random(0, 1677215);
    uint32_t _addr = random(0, flash.getCapacity());
#ifdef PRINTINDIVIDUALRUNS
    Serial.print("\t\t");
    Serial.print(x);
#endif

    if (flash.eraseSection(_addr, sizeof(configurationIn))) {
      //if (flash.eraseSector(_addr)) {
      eraseCount++;
#ifdef PRINTINDIVIDUALRUNS
      Serial.print("\t\t\t    Done");
#endif
    }
    else {
      eraseCount--;
    }
    /*if (flash.eraseSector(_addr)) {
      Serial.println("Sector has been erased");
      }*/
    if (flash.writeAnything(_addr, configurationIn)) {
#ifdef PRINTDETAIL
      Serial.println(configurationIn.lux);
      Serial.println(configurationIn.vOut);
      Serial.println(configurationIn.RLDR);
      Serial.println(configurationIn.light);
      Serial.println(configurationIn.adc);
      for (uint8_t i = 0; i < 8; i++) {
        Serial.print(configurationIn.arr[i]);
        Serial.print(",");
      }
      Serial.println();
      Serial.println(configurationIn.misc.tempHigh);
      Serial.println(configurationIn.misc.tempLow);
      Serial.println(configurationIn.misc.parkingMode);
      Serial.println(configurationIn.misc.allowDataToBeSent);
      for (uint8_t i = 0; i < 4; i++) {
        Serial.print(configurationIn.network.ssid[i]);
        Serial.print(",");
      }
      Serial.println();
      for (uint8_t i = 0; i < 3; i++) {
        Serial.print(configurationIn.network.pwd[i]);
        Serial.print(",");
      }
      Serial.println();
      for (uint8_t i = 0; i < 6; i++) {
        Serial.print(configurationIn.network.userid[i]);
        Serial.print(",");
      }
      Serial.println();
      Serial.println(configurationIn.charging.interval);
      Serial.println(configurationIn.charging.highChargingDefault);
#endif
      writeCount++;
      errorCount--;
#ifdef PRINTINDIVIDUALRUNS
      Serial.print("\t\t\t   Done\t\t\t\t   Pass");
#endif
    }
    else {
#ifdef PRINTINDIVIDUALRUNS
      Serial.print("\t\t\t   Done\t\t\t\t   Fail");
#endif
    }
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

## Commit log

2024-06-08 Adding CAD images
2024-06-08 Adding PCB files
    [Adafruit BNO055.brd, Adafruit BNO055.sch, MPL3115A2_v0.2.brd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]

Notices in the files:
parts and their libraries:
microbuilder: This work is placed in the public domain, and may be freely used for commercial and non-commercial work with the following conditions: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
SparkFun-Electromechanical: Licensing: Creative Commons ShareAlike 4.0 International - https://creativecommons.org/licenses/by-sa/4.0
